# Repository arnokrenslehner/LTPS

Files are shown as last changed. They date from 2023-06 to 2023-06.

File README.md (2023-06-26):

# LTPS
LTPS (**L**ow **T**emperature **P**ower **S**ystem) is a power supply board designed for high-altitude balloon applications.
It provides three step-up converters and load switches as well as an ADC which can be read via I2C. <br>
The smb connector on the upper left side is part of the "remove before flight" circuitry, you can use a shorted out smb plug to disable the whole
LTPS system.

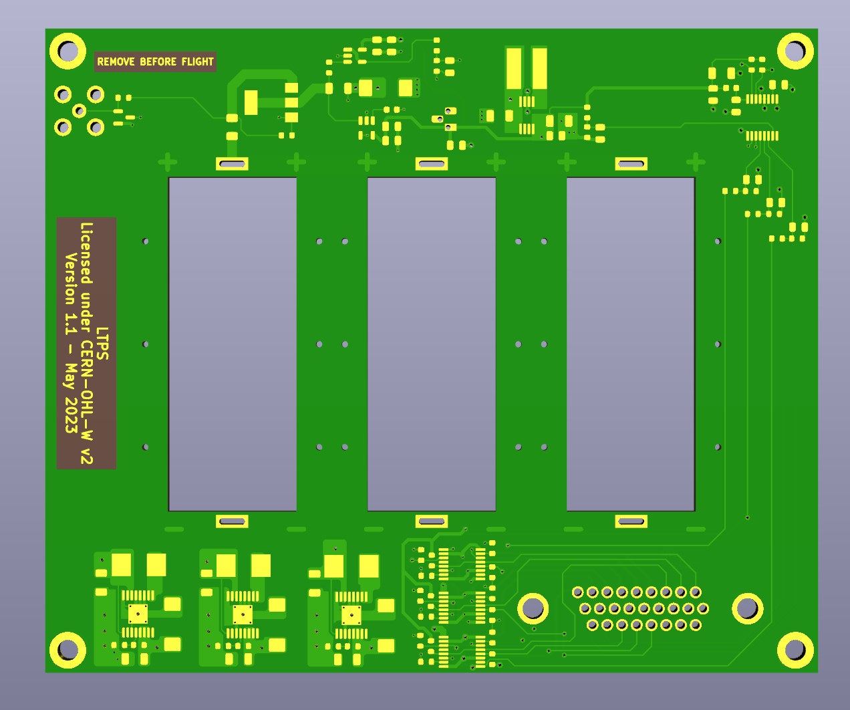
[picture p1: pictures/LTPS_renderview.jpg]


The board measures 120*100mm, its 4 layers.

## PCB Production and part procurement  
The design is optimized to the standard JLC-PCB 4-layer process.
I bought the parts from Mouser, all automotive types. Because it's just a private project 
I can't provide you with a "clean" BOM.

This version here incorporates all bugfixes from the first one I built:

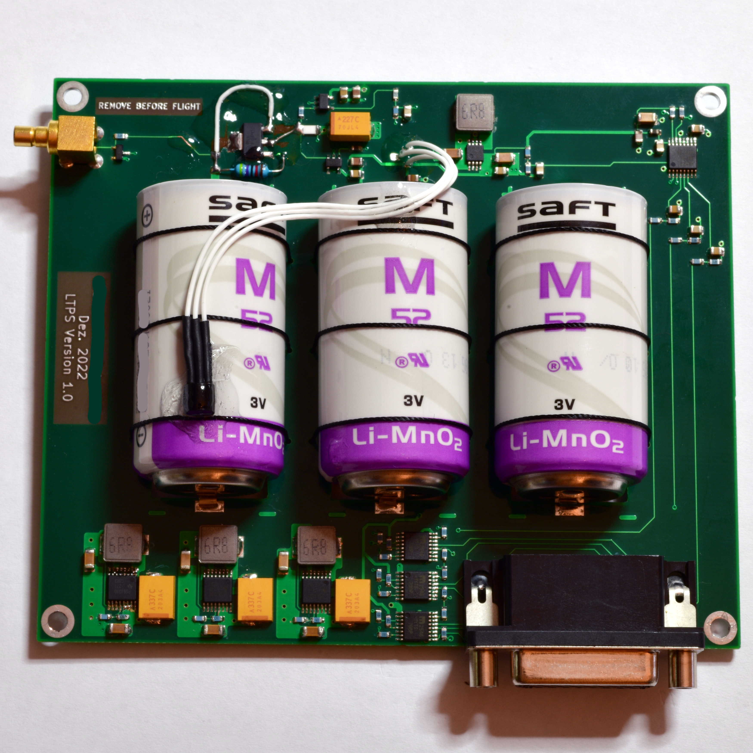
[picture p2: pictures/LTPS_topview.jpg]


One can see the bodge on the upper left of the PCB, I also fixed up some spacing, etc.

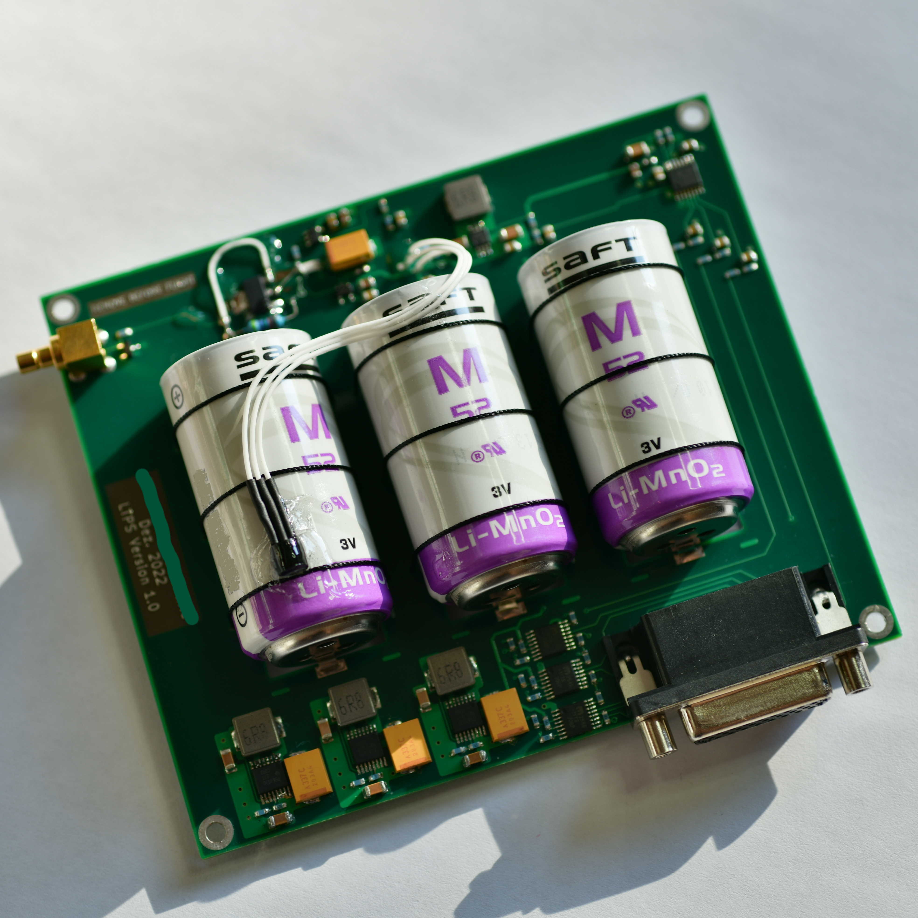
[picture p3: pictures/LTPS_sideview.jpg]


The board is designed to hold three "SAFT M52 LiMnO2" cells which are ideal for high-altitude ballooning, but expensive, one can 
use some other (lithium cells) in "C" size.

Please consult the schematic and the according datasheets for modifications etc.

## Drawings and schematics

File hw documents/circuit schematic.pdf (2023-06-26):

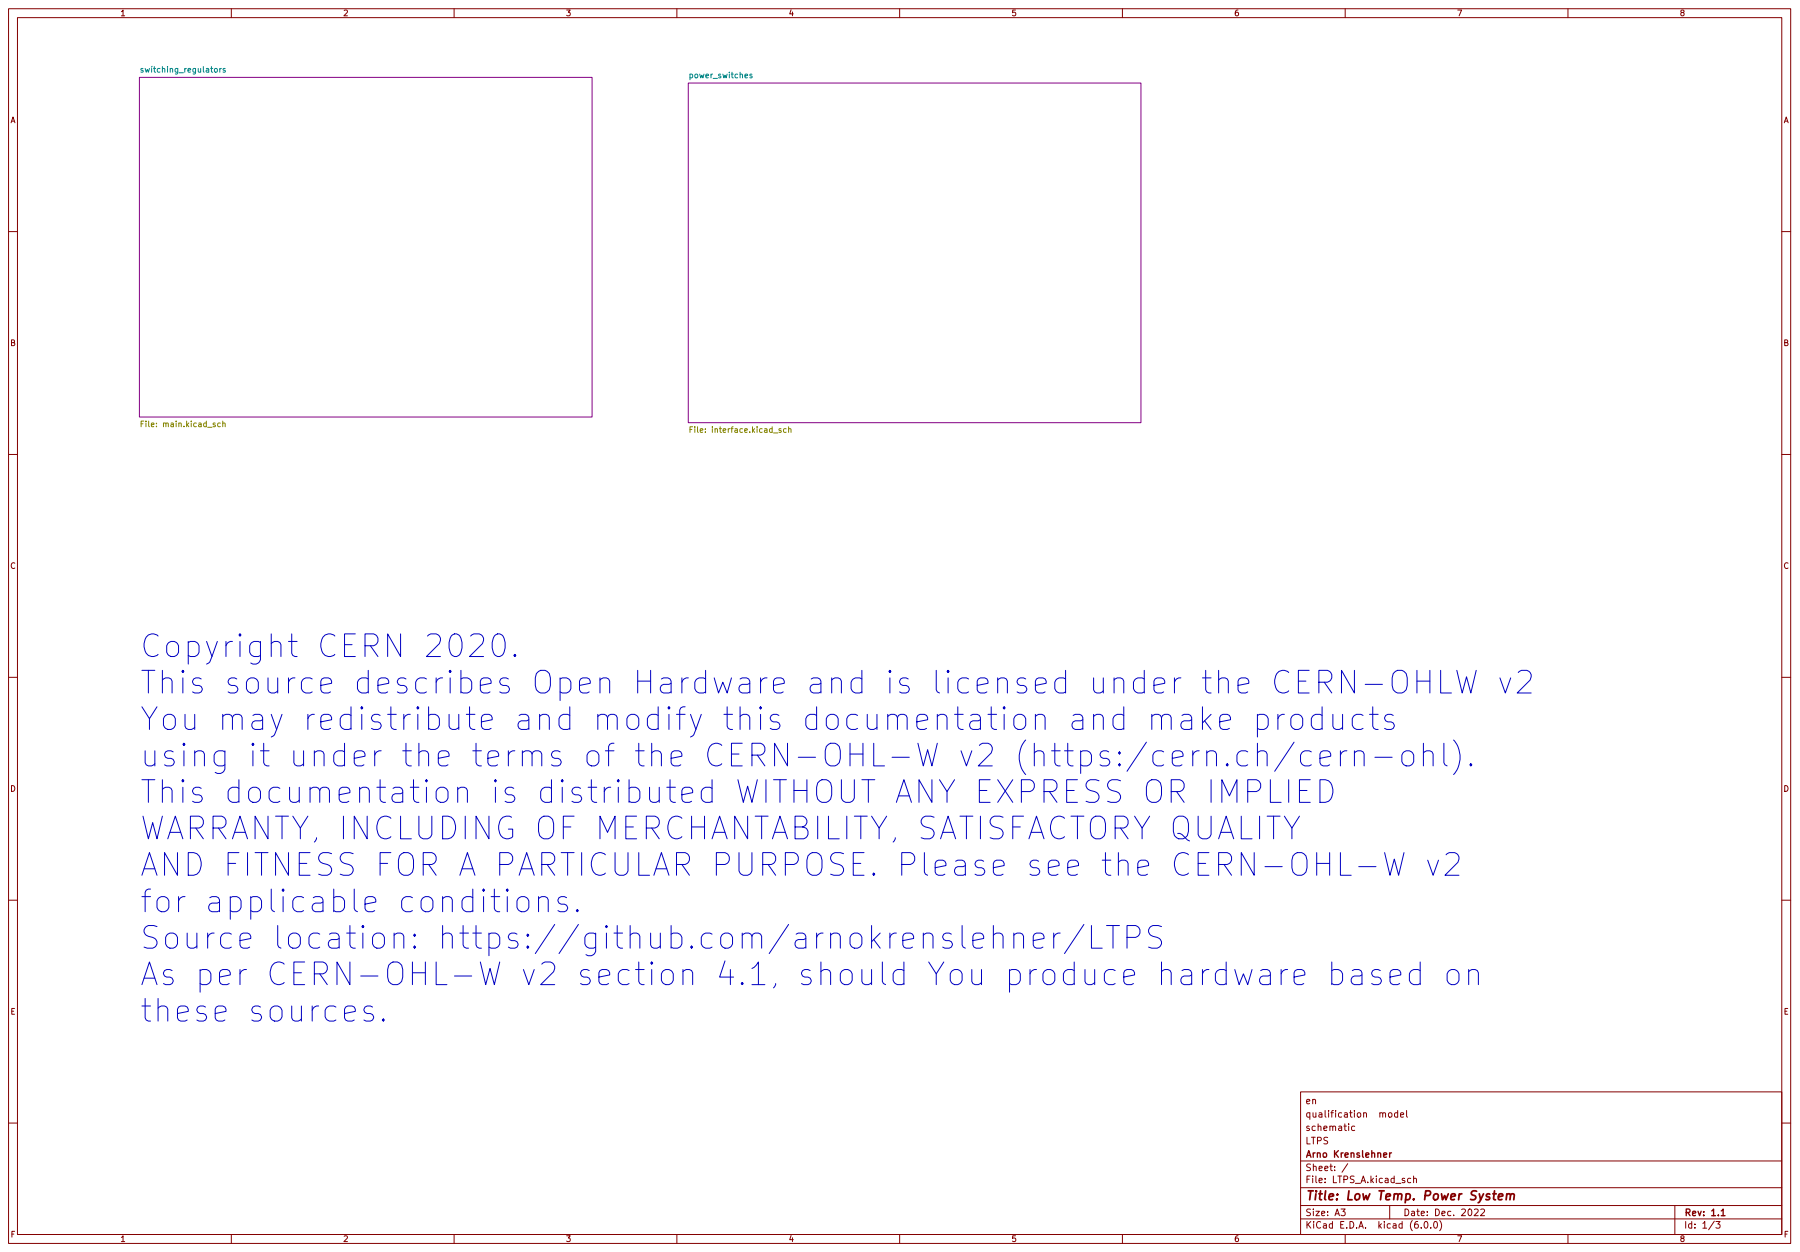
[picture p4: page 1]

þÿswítching_regulators File: main.kicad_sch
power_switches File: interface.kicad_sch Copyright CERN 2020.

This source describes Open Hardware and is licensed under the CERN-OHLW v2
You may redistribute and modify this documentation and make products
using it under the terms of the CERN-OHL-W v2 (https:/cern.ch/cern-ohl).
This documentation is distributed WITHOUT ANY EXPRESS OR IMPLIED
WARRANTY, INCLUDING OF MERCHANTABILITY, SATISFACTORY QUALITY
AND FITNESS FOR A PARTICULAR PURPOSE. Please see the CERN-OHL-W v2
for applicable conditions.
Source location: https://github.com/arnokrenslehner/LTPS
As per CERN-OHL-W v2 section 4.1, should You produce hardware based on
these sources.

schematic qualification model en

File: LTPS_A.kicad_sch Sheet: / Arno Krenslehner LTPS

Id: 1/3 Title: Low Temp. Power System

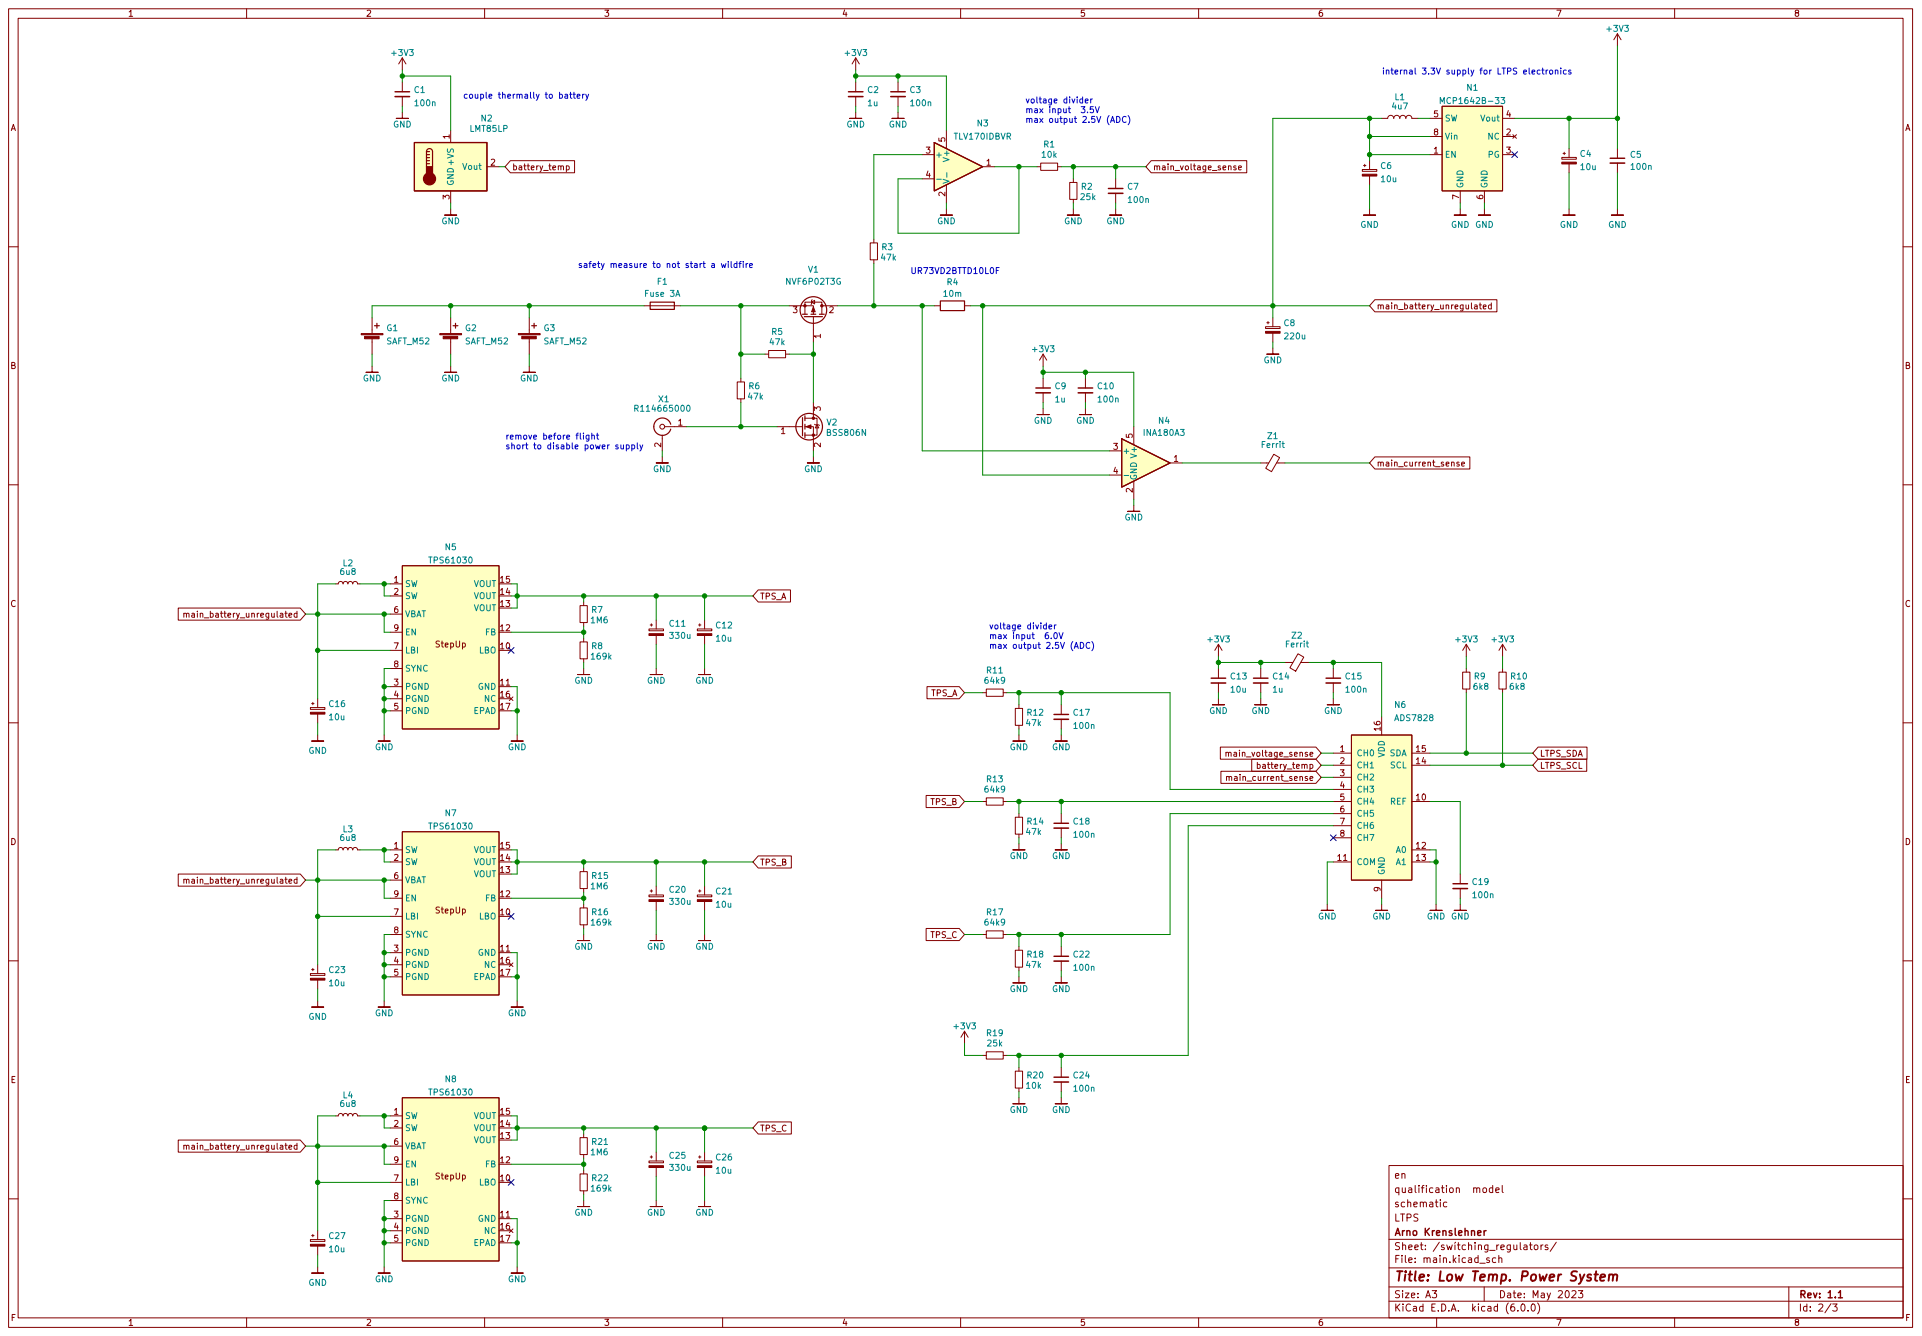
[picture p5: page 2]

internal 3.3V supply for LTPS electronics UR73VD2BTTD10L0F

couple thermally to battery

safety measure to not start a wildfire

remove before flight
short to disable power supply

schematic qualification model en

þÿSheet: /swítching_regulators/ Arno Krenslehner LTPS

File: main.kicad_sch
Id: 2/3 Title: Low Temp. Power System

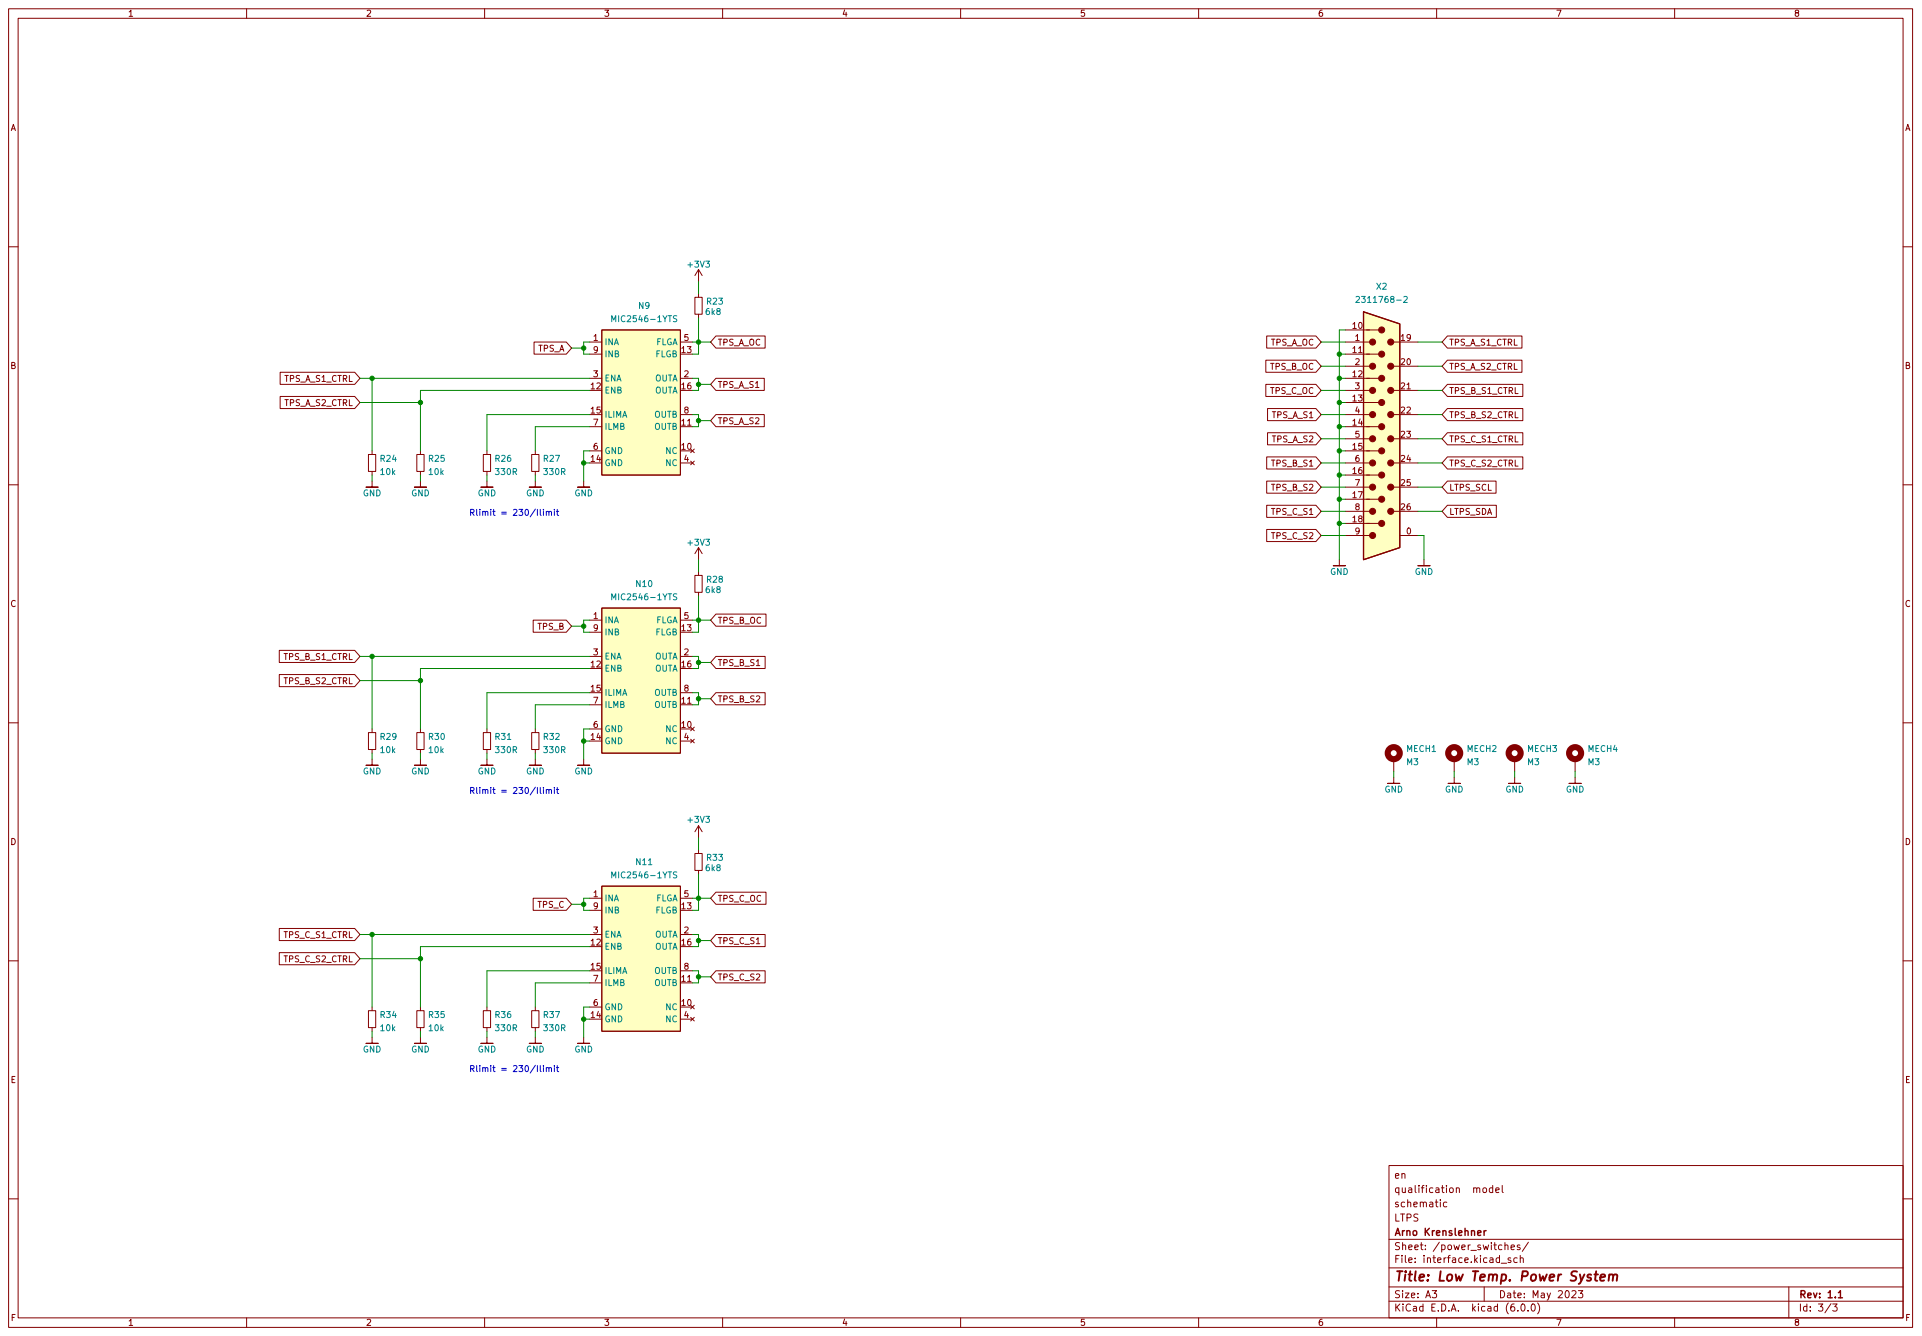
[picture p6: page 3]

schematic qualification model en

Sheet: /power_switches/ Arno Krenslehner LTPS

File: interface.kicad_sch
Id: 3/3 Title: Low Temp. Power System

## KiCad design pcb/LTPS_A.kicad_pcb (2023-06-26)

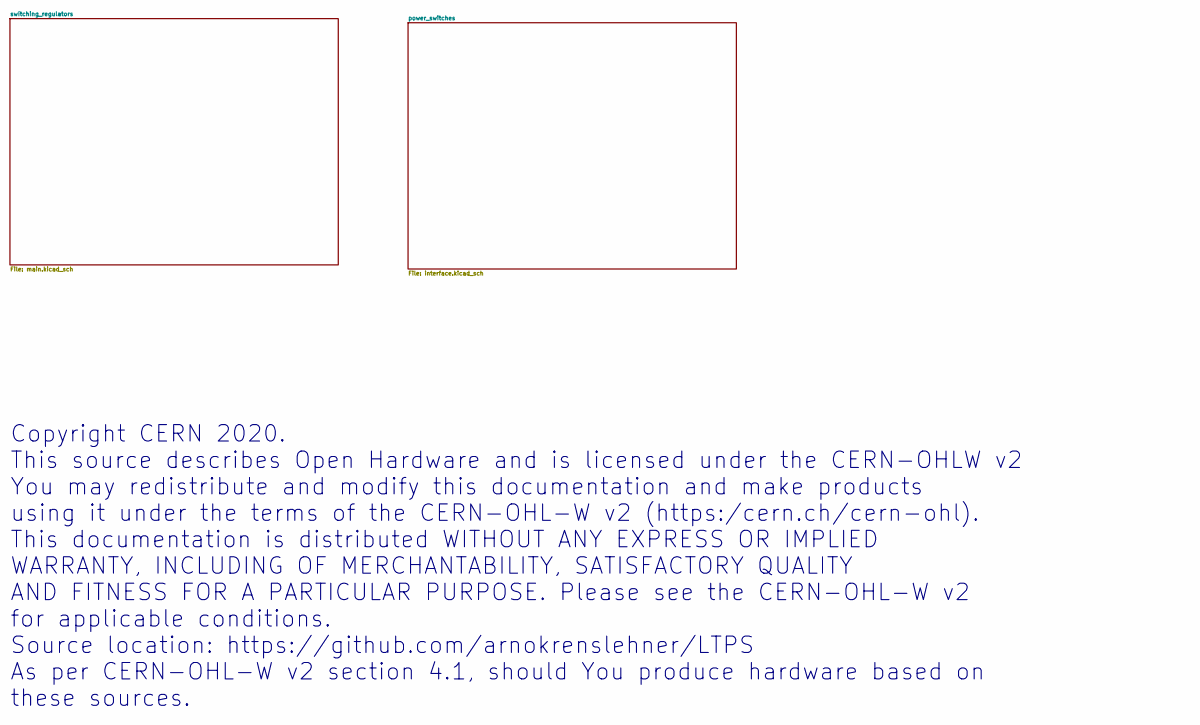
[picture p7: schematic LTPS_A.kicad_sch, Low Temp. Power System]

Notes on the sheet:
Copyright CERN 2020. This source describes Open Hardware and is licensed under the CERN-OHLW v2 You may redistribute and modify this documentation and make products using it under the terms of the CERN-OHL-W v2 (https:/cern.ch/cern-ohl). This documentation is distributed WITHOUT ANY EXPRESS OR IMPL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

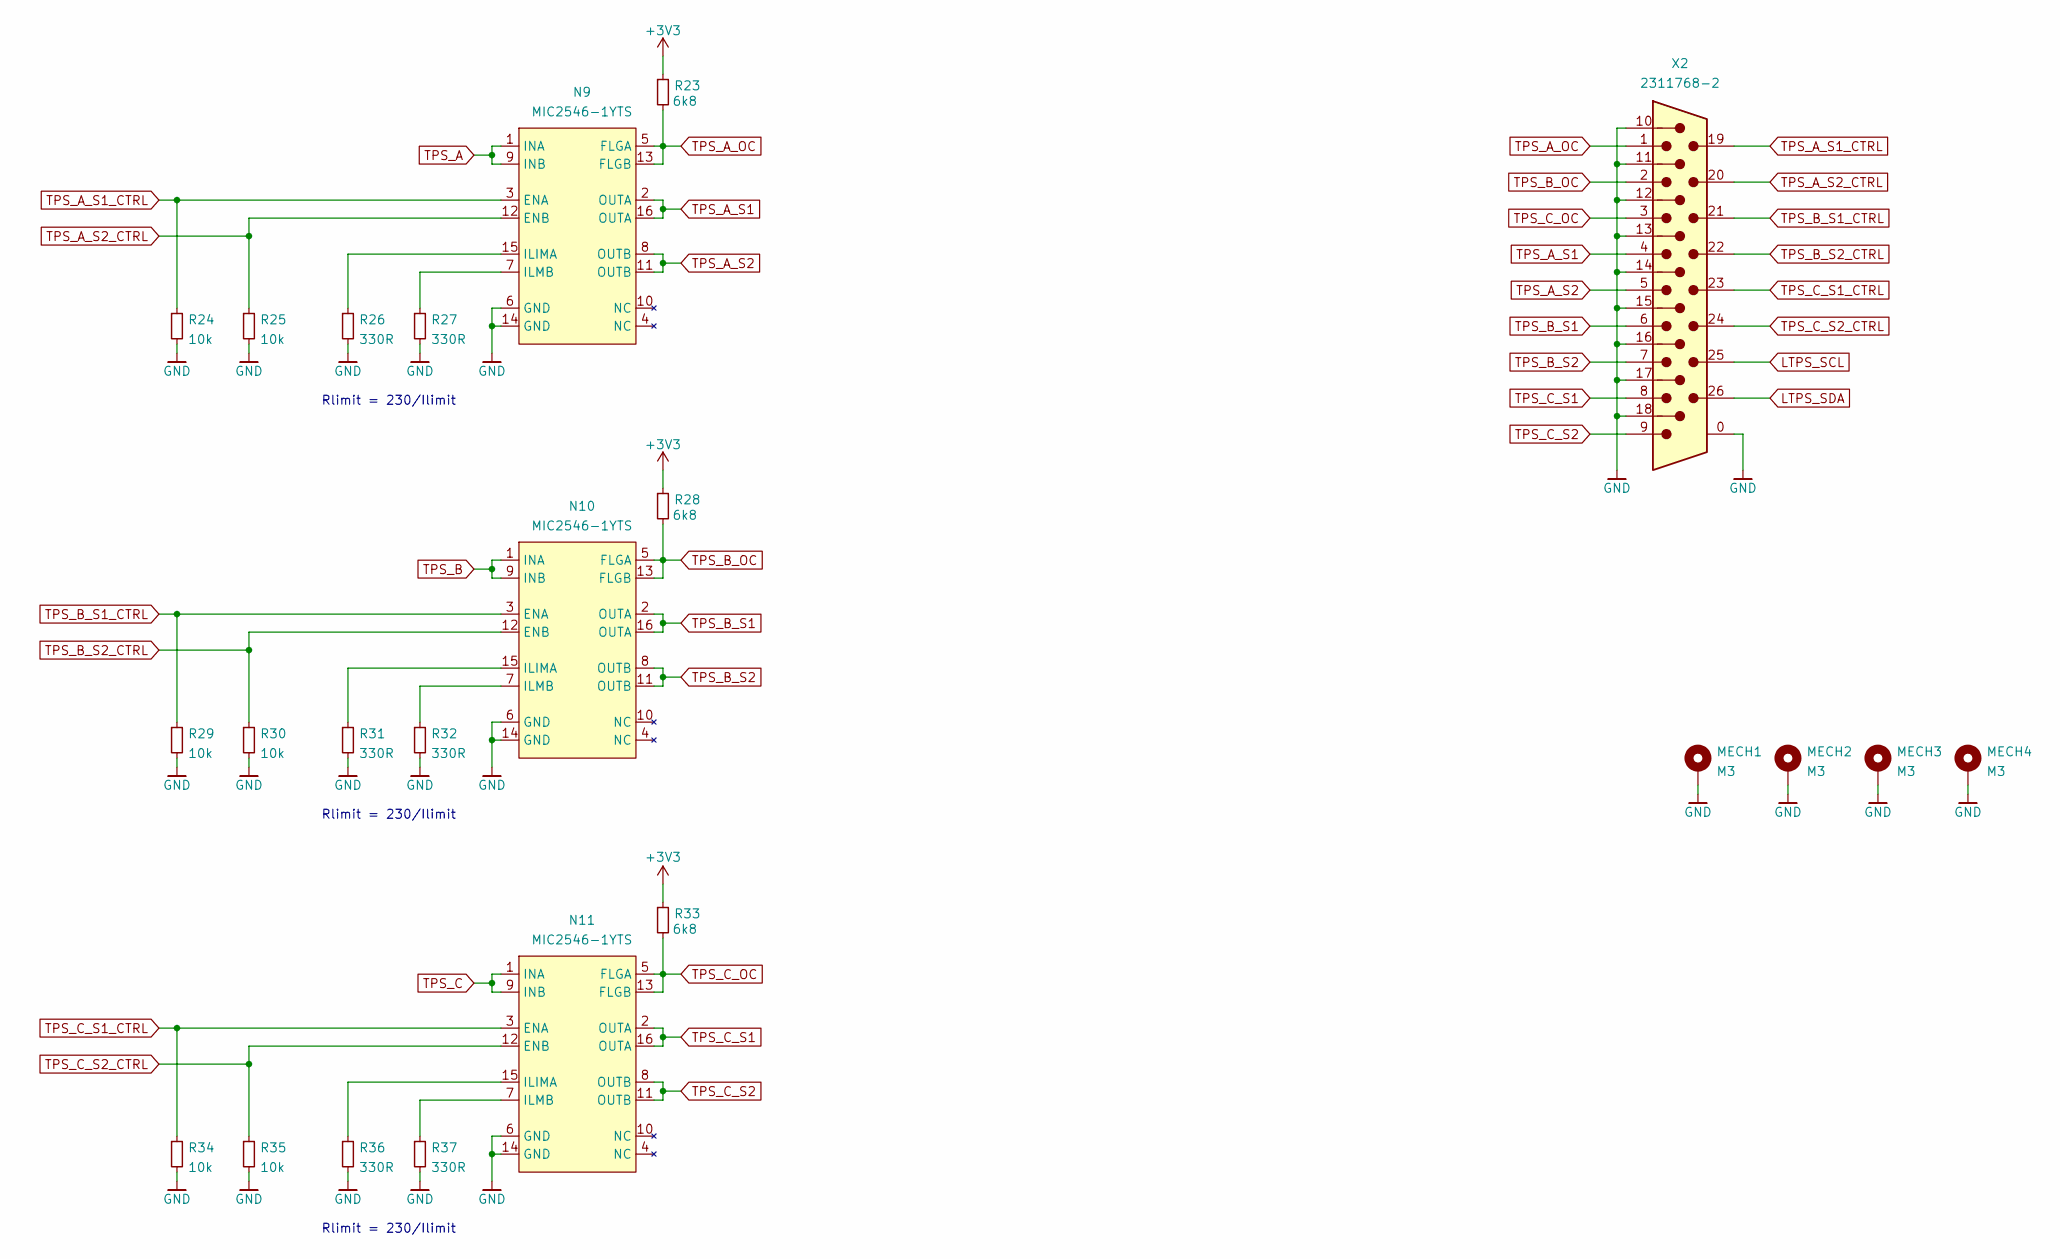
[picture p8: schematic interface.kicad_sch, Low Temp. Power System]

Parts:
MECH1, MECH2, MECH3, MECH4: M3; MountingHole_3.2mm_M3_ISO7380_Pad_TopBottom
N9, N10, N11: MIC2546-1YTS; TSSOP-16_4.4x5mm_P0.65mm
R23, R28, R33: 6k8; R_0603_1608Metric
R24, R25, R29, R30, R34, R35: 10k; R_0603_1608Metric
R26, R27, R31, R32, R36, R37: 330R; R_0603_1608Metric
X2: 2311768-2; 23117682

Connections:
+3V3: R23.1, R28.1, R33.1; also elsewhere on the board
GND: MECH1.1, MECH2.1, MECH3.1, MECH4.1, N9.6 (GND), N9.14 (GND), N10.6 (GND), N10.14 (GND), N11.6 (GND), N11.14 (GND), R24.2, R25.2, R26.2, R27.2, R29.2, R30.2, R31.2, R32.2, R34.2, R35.2, R36.2, R37.2, X2.0, X2.10, X2.11, X2.12, X2.13, X2.14, X2.15, X2.16, X2.17, X2.18; also elsewhere on the board
LTPS_SCL: X2.25; also elsewhere on the board
LTPS_SDA: X2.26; also elsewhere on the board
unnamed: N9.7 (ILMB), R27.1
unnamed: N9.15 (ILIMA), R26.1
unnamed: N10.7 (ILMB), R32.1
unnamed: N10.15 (ILIMA), R31.1
unnamed: N11.7 (ILMB), R37.1
unnamed: N11.15 (ILIMA), R36.1
TPS_A: N9.1 (INA), N9.9 (INB); also elsewhere on the board
TPS_A_OC: N9.5 (FLGA), N9.13 (FLGB), R23.2, X2.1
TPS_A_S1: N9.2 (OUTA), N9.16 (OUTA), X2.4
TPS_A_S1_CTRL: N9.3 (ENA), R24.1, X2.19
TPS_A_S2: N9.8 (OUTB), N9.11 (OUTB), X2.5
TPS_A_S2_CTRL: N9.12 (ENB), R25.1, X2.20
TPS_B: N10.1 (INA), N10.9 (INB); also elsewhere on the board
TPS_B_OC: N10.5 (FLGA), N10.13 (FLGB), R28.2, X2.2
TPS_B_S1: N10.2 (OUTA), N10.16 (OUTA), X2.6
TPS_B_S1_CTRL: N10.3 (ENA), R29.1, X2.21
TPS_B_S2: N10.8 (OUTB), N10.11 (OUTB), X2.7
TPS_B_S2_CTRL: N10.12 (ENB), R30.1, X2.22
TPS_C: N11.1 (INA), N11.9 (INB); also elsewhere on the board
TPS_C_OC: N11.5 (FLGA), N11.13 (FLGB), R33.2, X2.3
TPS_C_S1: N11.2 (OUTA), N11.16 (OUTA), X2.8
TPS_C_S1_CTRL: N11.3 (ENA), R34.1, X2.23
TPS_C_S2: N11.8 (OUTB), N11.11 (OUTB), X2.9
TPS_C_S2_CTRL: N11.12 (ENB), R35.1, X2.24

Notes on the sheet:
Rlimit = 230/Ilimit

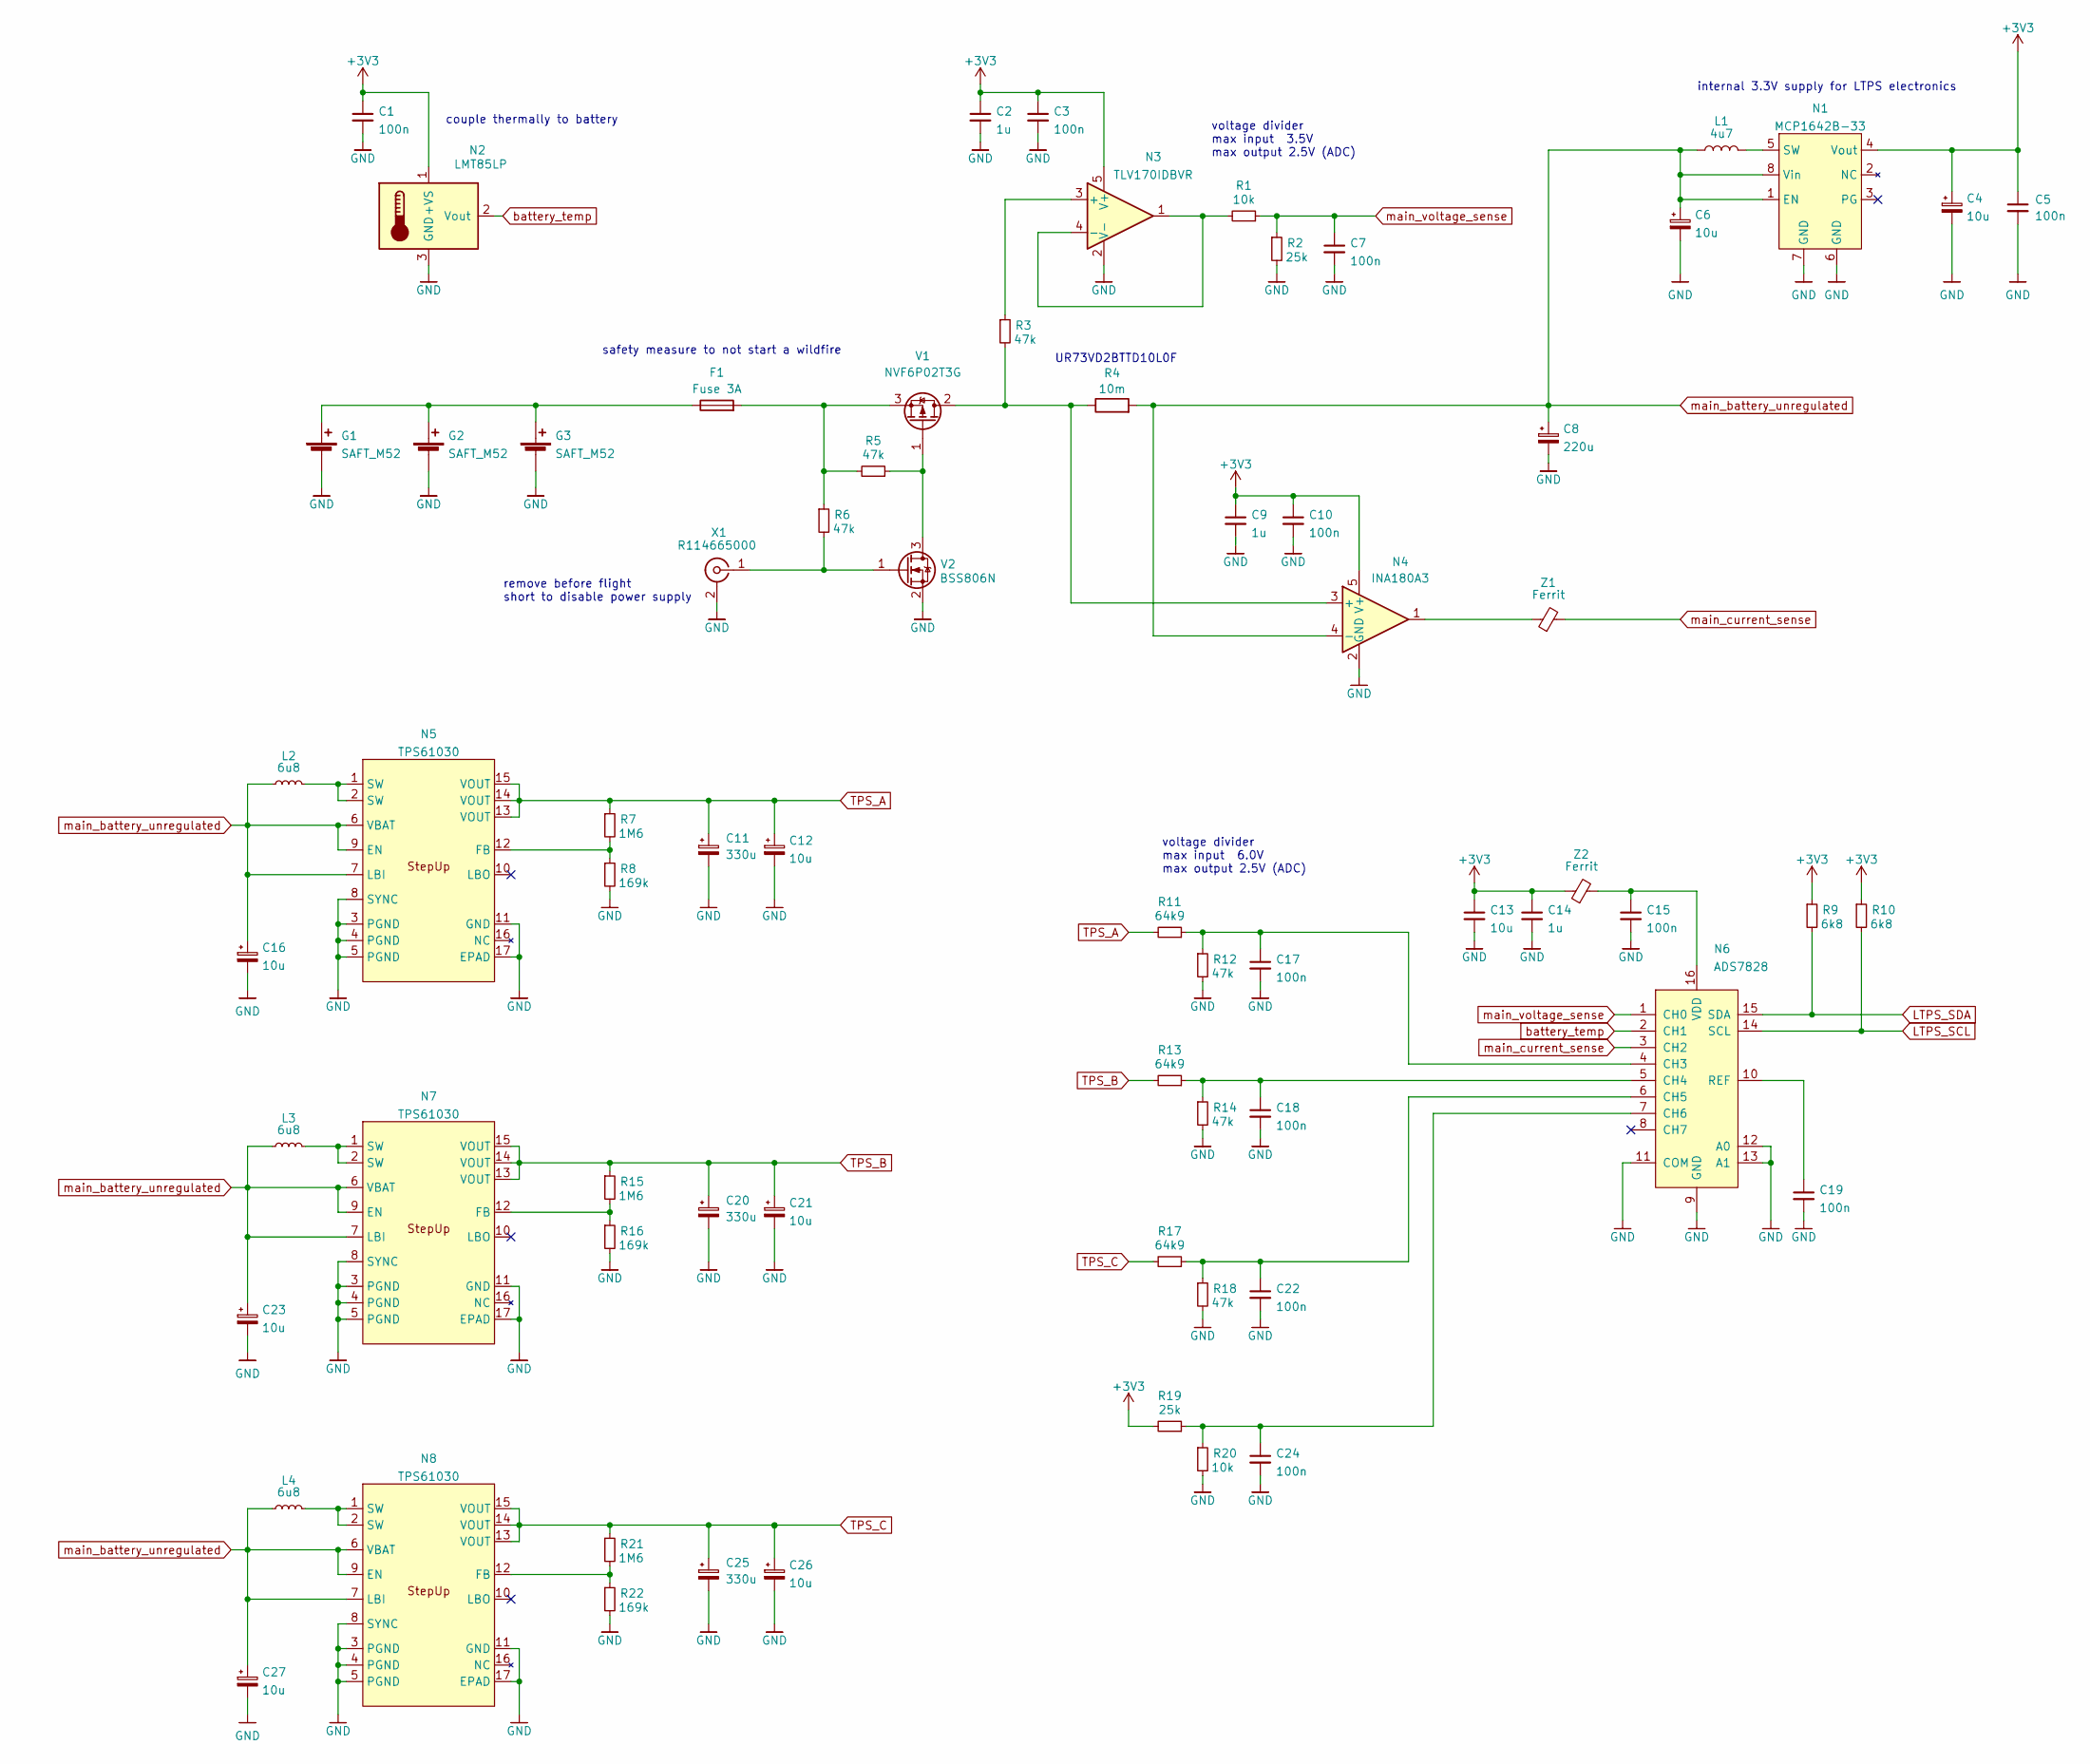
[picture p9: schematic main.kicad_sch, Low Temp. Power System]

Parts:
C1, C3, C5, C7, C10, C15, C17, C18, C19, C22, C24: 100n; C_0805_2012Metric
C2, C9, C14: 1u; C_0805_2012Metric
C4, C6, C12, C13, C16, C21, C23, C26, C27: 10u; C_1206_3216Metric
C8: 220u; CP_EIA-7343-30_AVX-N
C11, C20, C25: 330u; CP_EIA-7343-30_AVX-N
F1: Fuse 3A; Fuse_1206_3216Metric
G1, G2, G3: SAFT_M52
L1: 4u7; WE-TPC_5818_582892
L2, L3, L4: 6u8; L_Bourns_SRP7028A_7.3x6.6mm
N1: MCP1642B-33; MSOP-8_3x3mm_P0.65mm
N2: LMT85LP; TO-92_HandSolder
N3: TLV170IDBVR; TSOT-23-5
N4: INA180A3; SOT-23-5
N5, N7, N8: TPS61030; TSSOP-16-1EP_4.4x5mm_P0.65mm_EP3x3mm_ThermalVias
N6: ADS7828; TSSOP-16_4.4x5mm_P0.65mm
R1, R20: 10k; R_0603_1608Metric
R2, R19: 25k; R_0603_1608Metric
R3, R5, R6, R12, R14, R18: 47k; R_0603_1608Metric
R4: 10m; R_1206_3216Metric
R7, R15, R21: 1M6; R_0603_1608Metric
R8, R16, R22: 169k; R_0603_1608Metric
R9, R10: 6k8; R_0603_1608Metric
R11, R13, R17: 64k9; R_0603_1608Metric
V1: NVF6P02T3G; SOT-223-3_TabPin2
V2: BSS806N; SOT-23
X1: R114665000; SMB_Jack_Vertical
Z1, Z2: Ferrit; L_0603_1608Metric

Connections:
+3V3: C1.1, C2.1, C3.1, C4.1, C5.1, C9.1, C10.1, C13.1, C14.1, N1.4 (Vout), N2.1 (+VS), N3.5 (V+), N4.5 (V+), R9.1, R10.1, R19.2, Z2.1; also elsewhere on the board
GND: C1.2, C2.2, C3.2, C4.2, C5.2, C6.2, C7.2, C8.2, C9.2, C10.2, C11.2, C12.2, C13.2, C14.2, C15.2, C16.2, C17.2, C18.2, C19.2, C20.2, C21.2, C22.2, C23.2, C24.2, C25.2, C26.2, C27.2, G1.2 (-), G2.2 (-), G3.2 (-), N1.6 (GND), N1.7 (GND), N2.3 (GND), N3.2 (V-), N4.2 (GND), N5.3 (PGND), N5.4 (PGND), N5.5 (PGND), N5.8 (SYNC), N5.11 (GND), N5.17 (EPAD), N6.9 (GND), N6.11 (COM), N6.12 (A0), N6.13 (A1), N7.3 (PGND), N7.4 (PGND), N7.5 (PGND), N7.8 (SYNC), N7.11 (GND), N7.17 (EPAD), N8.3 (PGND), N8.4 (PGND), N8.5 (PGND), N8.8 (SYNC), N8.11 (GND), N8.17 (EPAD), R2.2, R8.2, R12.2, R14.2, R16.2, R18.2, R20.2, R22.2, V2.2 (S), X1.2 (Ext); also elsewhere on the board
LTPS_SCL: N6.14 (SCL), R10.2; also elsewhere on the board
LTPS_SDA: N6.15 (SDA), R9.2; also elsewhere on the board
unnamed: C15.1, N6.16 (VDD), Z2.2
unnamed: C17.1, N6.4 (CH3), R11.1, R12.1
unnamed: C18.1, N6.5 (CH4), R13.1, R14.1
unnamed: C19.1, N6.10 (REF)
unnamed: C22.1, N6.6 (CH5), R17.1, R18.1
unnamed: C24.1, N6.7 (CH6), R19.1, R20.1
unnamed: F1.1, G1.1 (+), G2.1 (+), G3.1 (+)
unnamed: F1.2, R5.2, R6.1, V1.3 (S)
unnamed: L1.2, N1.5 (SW)
unnamed: L2.2, N5.1 (SW), N5.2 (SW)
unnamed: L3.2, N7.1 (SW), N7.2 (SW)
unnamed: L4.2, N8.1 (SW), N8.2 (SW)
unnamed: N3.1, N3.4 (-), R1.2
unnamed: N3.3 (+), R3.1
unnamed: N4.1, Z1.1
unnamed: N4.3 (+), R3.2, R4.1, V1.2 (D)
unnamed: N5.12 (FB), R7.2, R8.1
unnamed: N7.12 (FB), R15.2, R16.1
unnamed: N8.12 (FB), R21.2, R22.1
unnamed: R5.1, V1.1 (G), V2.3 (D)
unnamed: R6.2, V2.1 (G), X1.1 (In)
TPS_A: C11.1, C12.1, N5.13 (VOUT), N5.14 (VOUT), N5.15 (VOUT), R7.1, R11.2; also elsewhere on the board
TPS_B: C20.1, C21.1, N7.13 (VOUT), N7.14 (VOUT), N7.15 (VOUT), R13.2, R15.1; also elsewhere on the board
TPS_C: C25.1, C26.1, N8.13 (VOUT), N8.14 (VOUT), N8.15 (VOUT), R17.2, R21.1; also elsewhere on the board
battery_temp: N2.2 (Vout), N6.2 (CH1)
main_battery_unregulated: C6.1, C8.1, C16.1, C23.1, C27.1, L1.1, L2.1, L3.1, L4.1, N1.1 (EN), N1.8 (Vin), N4.4 (-), N5.6 (VBAT), N5.7 (LBI), N5.9 (EN), N7.6 (VBAT), N7.7 (LBI), N7.9 (EN), N8.6 (VBAT), N8.7 (LBI), N8.9 (EN), R4.2
main_current_sense: N6.3 (CH2), Z1.2
main_voltage_sense: C7.1, N6.1 (CH0), R1.1, R2.1

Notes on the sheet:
couple thermally to battery
internal 3.3V supply for LTPS electronics
UR73VD2BTTD10L0F
safety measure to not start a wildfire
voltage divider max input 3.5V max output 2.5V (ADC)
remove before flight short to disable power supply
voltage divider max input 6.0V max output 2.5V (ADC)

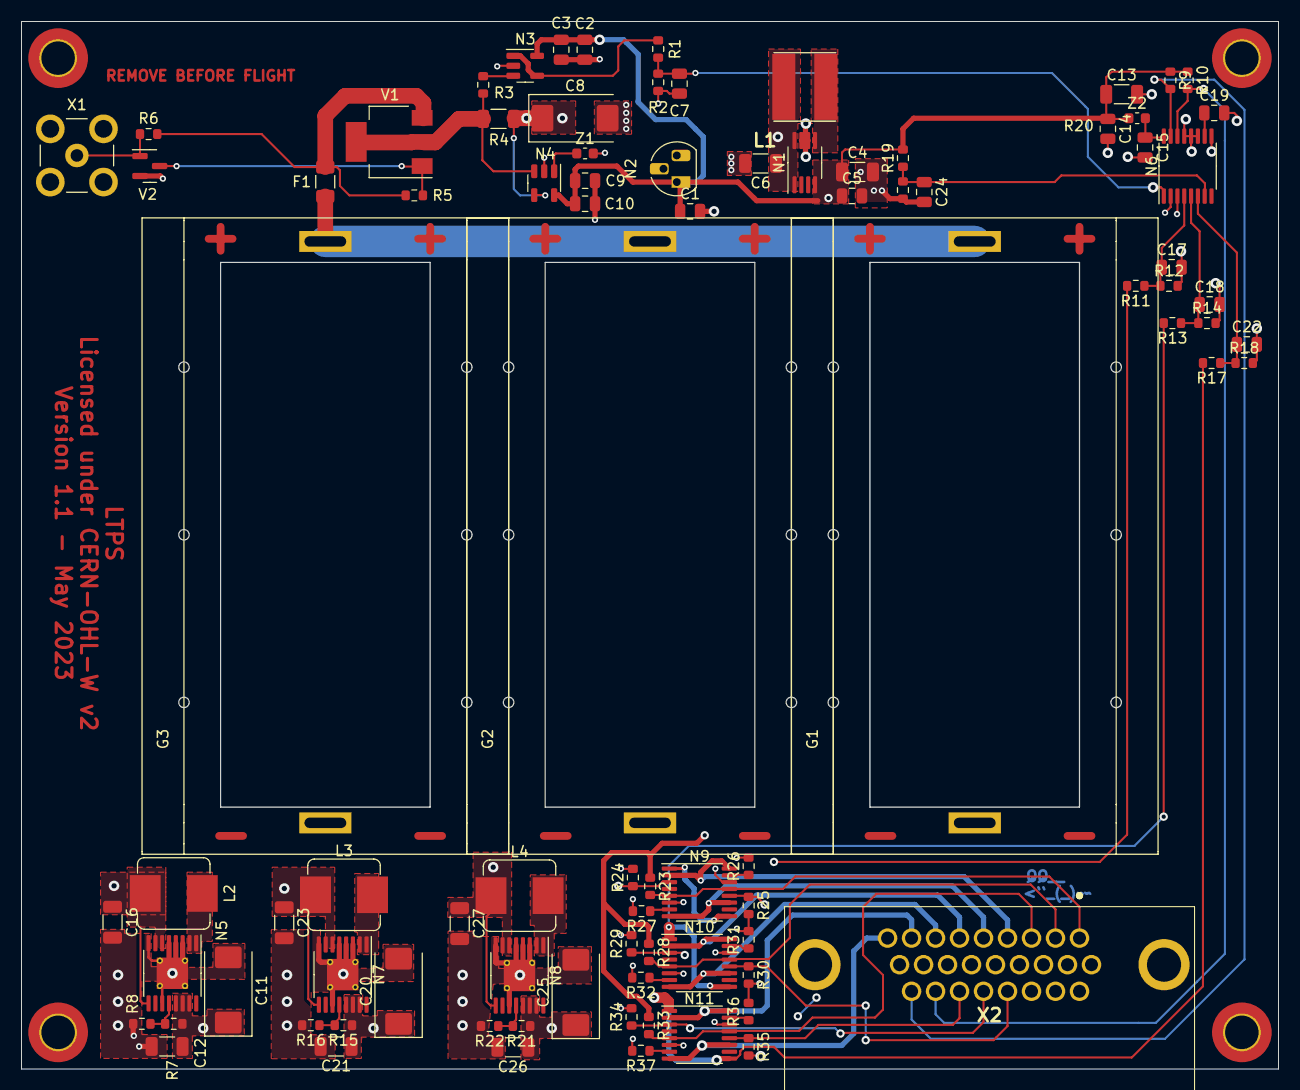
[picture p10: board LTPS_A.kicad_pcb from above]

Board: 4 copper layers, 120.0 x 100.0 mm, 93 parts (0 on the bottom side), 53 nets.

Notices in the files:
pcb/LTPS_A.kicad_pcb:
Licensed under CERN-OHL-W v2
